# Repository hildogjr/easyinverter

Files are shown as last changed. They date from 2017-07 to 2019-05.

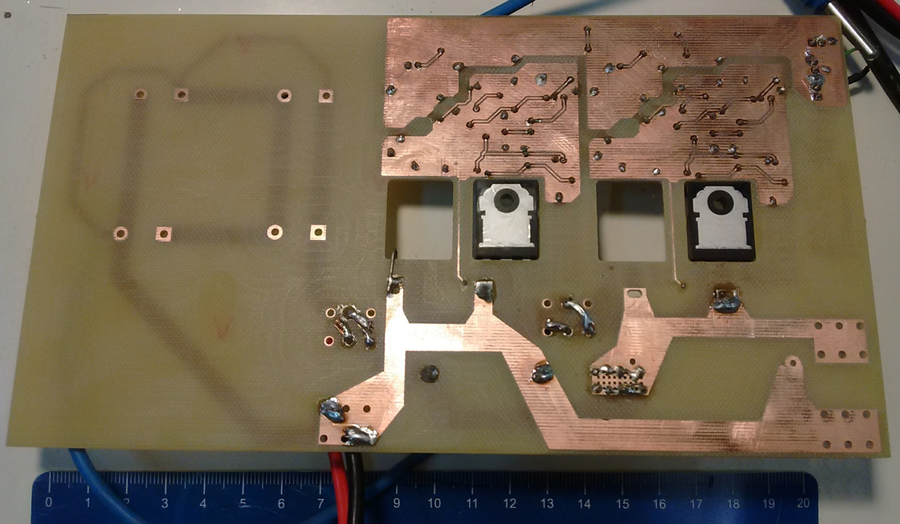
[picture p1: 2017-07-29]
prj v1/Assemblies/2017-03-13 One phase prototype [HGJr]/2017-04-28_OnePhase2(bottom).jpg

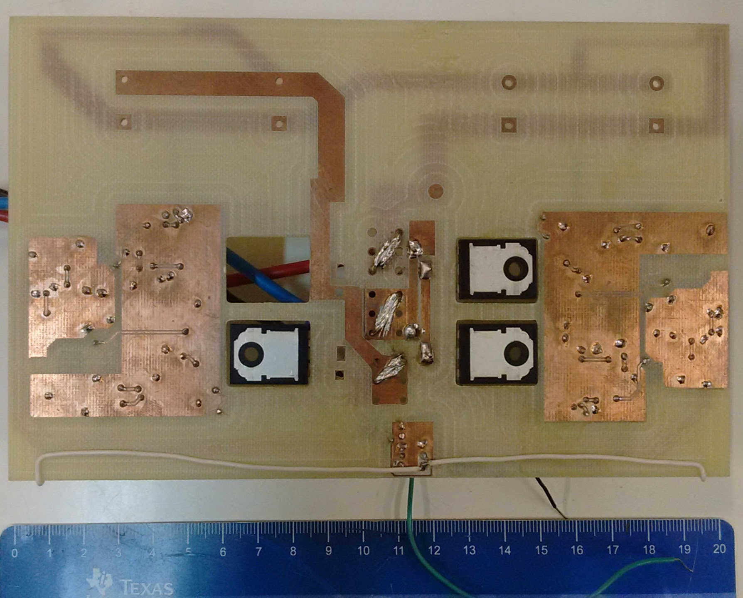
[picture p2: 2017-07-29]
prj v1/Assemblies/2017-04-03_OnePhase(bottom).jpg

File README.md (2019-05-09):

# EasyInverter
**An academic budget cost modular 4 arms inverter focused to use in researches**

Initial development by Power Conditioning Laboratory (*[Laboratório de Condicionamento da Energia Elétrica](http://www.fee.unicamp.br/dse/antenor/lcee)*), [School of Electrical and Computer Engineering](http://www.fee.unicamp.br/?language=en), at University of Campinas ([**UNICAMP Brazil**](http://www.unicamp.br/unicamp/english)).

The use of this project is free and conditioned to GNU General Propose License 3.0. The financial support was provide by São Paulo Research Foundation (FAPESP) under grants 2014/11720-7 and 2015/02325-0.

The publication of academics works contend results using this project if conditioned to a ACKNOWLEDGMENT and citation of this repository in the "acknowledgment part" of the article/paper.

You may use this text:
"The authors are grateful to the EdgeVerter's work team by the inverter project, which is available at <<https://github.com/hildogjr/EdgeVerter>>"

The GERBERs and schematic PDF are provided in the [Assemblies folder](/Assemblies).

The most recent files was designed using [Altium 18](http://www.altium.com/).

The Cost Bill of Materials can be updated by [``kicost -w -i BoM.xml -eda altium``](https://xesscorp.github.io/KiCost/), installing by ``python -m pip install kicost``.

---

## Max values (limitation) / general specifications
The specification values are not necessary concomitant.

- 10kW processing power;
- 600V of DC link;
- 50A in one phase;
- 200kHz switching frequency;
- 3.3V or 5V input logic control;
- Min dead-time & phase transistors interlock on-board;
- TWO extra relays;
- SMD topology with TO-247 transistor to easy replacement;
- Isolated power supplier to the gate driver (it not depends of PWM to works fine);
- Protection: under voltage of the isolated supplier (gate driver), over current, over voltage on the group of transistors and over temperature.

## Predicted powers proposes (look in power limitations)
1. 800V/10A -> To inverters grid connected applications, motor control;
2. 400V/30A -> To inverters grid connected applications, motor control;
3. 100V/100A -> DC/DC converters.

## Predicted uses, studies of
1. DC/DC converters, e.g., boost, buck, buck-boost, push-pull;
2. Power switching supplies, isolated topologies based on DC/DC converters;
3. Resonant converters;
4. Single-phase inverter, using the two first arms. Possibility to use the 3rd arm to synchronous connection to the grid and 4th to DC link boost/pre-load/discharge (discharge, pre-load and connection may be also performed by the two relays);
5. Three-phase inverter three wire connection. With possibility of extra arm to pre-load/discharge of the DC link, DC/DC boost or any extra application connected to the same DC link;
6. Three-phase inverter four wire connection (three-phase plus neutral);
7. Single-phase back-to-back inverter (to three-phase is necessary use two boards);
8. DOUBLE isolated single-phase inverters (independent DC links), to use as multilevel inverter applications;
9. Three-phase Vienna rectifier.

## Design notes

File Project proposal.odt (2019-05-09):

Projeto Inversor LCEE

RESUMO

Projeto do hardware de um inversor para ser utilizado em projetos de pesquisa no LCEE.

OBJETIVOS

1. O hardware deve ser robusto e projetado para evitar falhas e erros de operação, para tanto, deve utilizar proteções e indicar claramente ao usuário quando uma proteção for acionada, além de enviar sinal ao sistema de controle.
2. O hardware deve ser projetado para imunidade à interferência eletromagnética. Sendo todos os sinais de comando e retroação (proteção ativada) isolados da parte de potência.
3. O hardware deve ser flexível para atender, ao máximo possível, uma gama projetos de P&D encontrada no laboratório LCEE da Unicamp.
4. O hardware deve facilitar a obtenção de resultados experimentais, permitindo fácil acesso aos sinais internos (pontos de prova de tensão e corrente devem ser providos).

ESPECIFICAÇÕES

Tensão / Corrente

Proposta 1: 800V/10A

Proposta 2: 400V/30A

Proposta 3: 100V/100A

Frequencia de comutação:

Proposta 1: 200kHz

Outras propostas:

- Para mudança nas specs de tensão/corrente, trocar apenas transistores, resistores de gate e configurar proteção.
- Não utilizar circuto de bootstrap (possibilidade de acionar chave inferior e superior de modo independente).
- Auto-diagnóstico do estado da chave de potência.
- Tensão negativa para desligamento da chave.
- Possibilidade de utilização de transistores em SiC.
- Escalável / modular.
- Facilidade para conexão em diferentes aplicações, como inversor, inversor multinível, fonte chaveada etc.
- Proteção de mínimo dead-time.
- Modularidade na quantidade de braços.

MILESTONES/CRONOGRAMA

Reuniões de Alinhamento

Reunião 2 realizada dia 19/04/2016.

Reunião 3 realizada dia 06/05/2016.

Reunião 4 realizada dia 24/05/2016.

Distribuições de tarefas

Ficaram divididas as seguintes frentes para avançar o projeto:

1. Fonte isolada / driver => Responsável: Joel
2. Seleção do mosfet e proteção dos MOSFETs => Responsável: Lais
3. Circuitos lógicos e isolação => Responsável: Hildo
4. Montagem da placa anterior => Responsável: JP

Aplicações

Tendo em vista que a placa terá 4 braços de MOSFETs, abaixo são listadas as aplicações típica em que ela poderá ser utilizada. A placa possuirá 2 barramentos CC que poderão ser conectados de forma paralela ou independente, além de 2 saídas auxiliares a transistor para conexão de relês em 12V.

Para uso da descarga/pré-carga será necessário o uso de resistores externos e para o uso da chave rápida de conexão a rede, diodos externos.

1. Conversores CC/CC em geral. Exemplos: boost, buck, buck-boost, push-pull;
2. Fontes chaveadas, arquiteturas baseadas nos conversores CC/CC mais push-pull e full bridge;
3. Conversores resonantes;
4. Inversor monofásico (usando os braços A-B e com possibilidade de uso do braço C para conexão sincronizada a rede e braço N para descarga/pré-carga do barramento CC, essa última função também pode ser realizada pelos relês externos);
5. Inversor trifásico a 3 fios (com possibilidade de uso do 4º braço para descarga/pré-carga do barramento CC, por exemplo, no caso de acionamento de motores, descarregar o barramento no uso de frenagem eletromagnética);
6. Inversor trifásico a 4 fios;
7. Back-to-back monofásico (para trifásico usar duas placas);
8. Duplo inversor monofásico isolados entre si (para conexão série pelo lado CA e aplicações em multinível).

Escolha dos transistores

Definido encapsulamento TO-247

Modelos escolhidos:

Part# | Fabrica. | USD | Vds | Id | Qg | Tr+Tf

Escolha do gate driver

Modelo, corrente, tempos de atraso para a chave escolhida etc…

Opção inicial: MIC4420

Alternativas: MIC4421 (mais rápido), TC4420, MAX4420

Isolação do transistor / driver

Modelo de isoladores, tempos de atraso, etc:

Opção inicial: Si8422

Alternativa: FOD8012

Projeto da fonte do driver

Considerando:

N (número de chaves em paralelo) = 2

Vd (tensãod e alimentação do driver) = 12V

Qg (gate charge máximo por chave) = 234nC

Fs (frequencia máxima de comutação) = 200kHz

Por driver:

P = N * Vd * Qg * Fs = 2 * 12V * 234nC * 200kHz = 1,12W

Supondo que a proteção, isolação, driver, tenha consumo de 150mW, temos a potência por fonte de driver de 1,3W.

Projeto da fonte principal

Como ponto de partida, a potencia de cada fonte do driver de 1,3W, e supondo uma eficiência de 0.66 da fonte, no primário é cerca de 1,9W. Com 8 canais, são 15,2W. Mais os circuitos lógicos/ proteção na entrada, podemos estimar uns 3W. São então 18W, ou seja, precisamos cerca de 1,5A no 12V.

Prever mais 90 a 150mA máximo por saída de relê auxiliar, totalizando mais 300mA. Modelos interessantes: T9A series (90mA@12V) e automotivos em geral (140mA@12V).

Projeto térmico

Pesquisar dissipadores em www.tctbrasil.com.br. Definir temperatura do dissipador, ventilação etc.

Tentar casar dimensão de placa com um único dissipador.

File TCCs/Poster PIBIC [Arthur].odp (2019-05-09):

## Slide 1

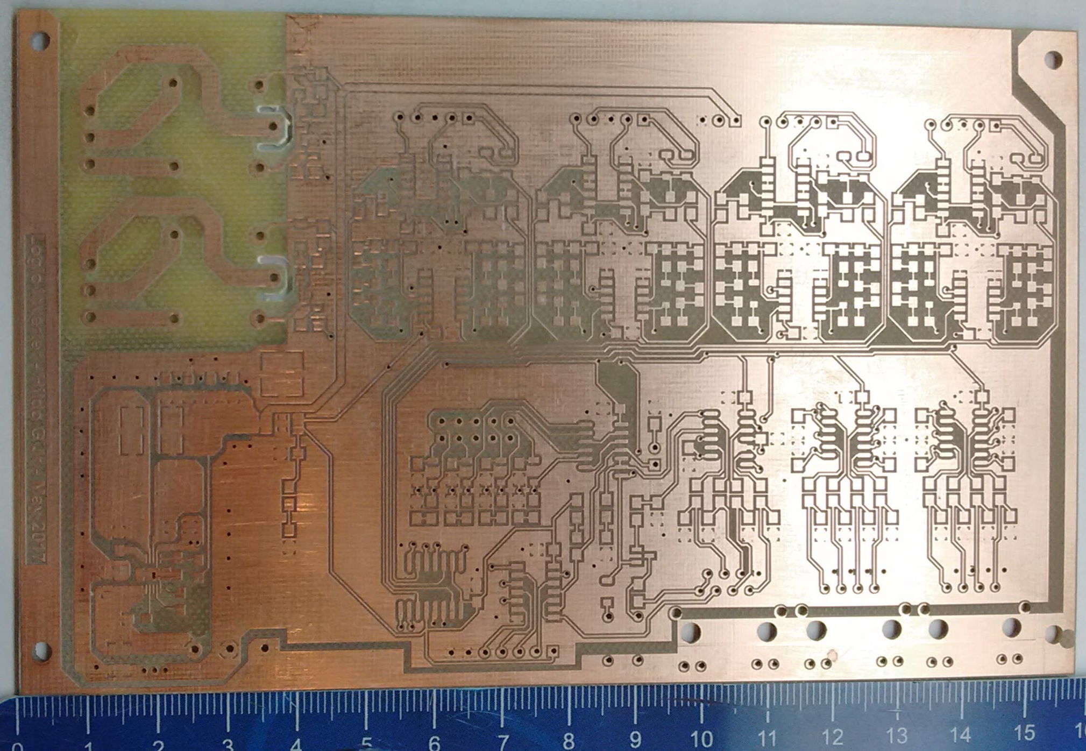
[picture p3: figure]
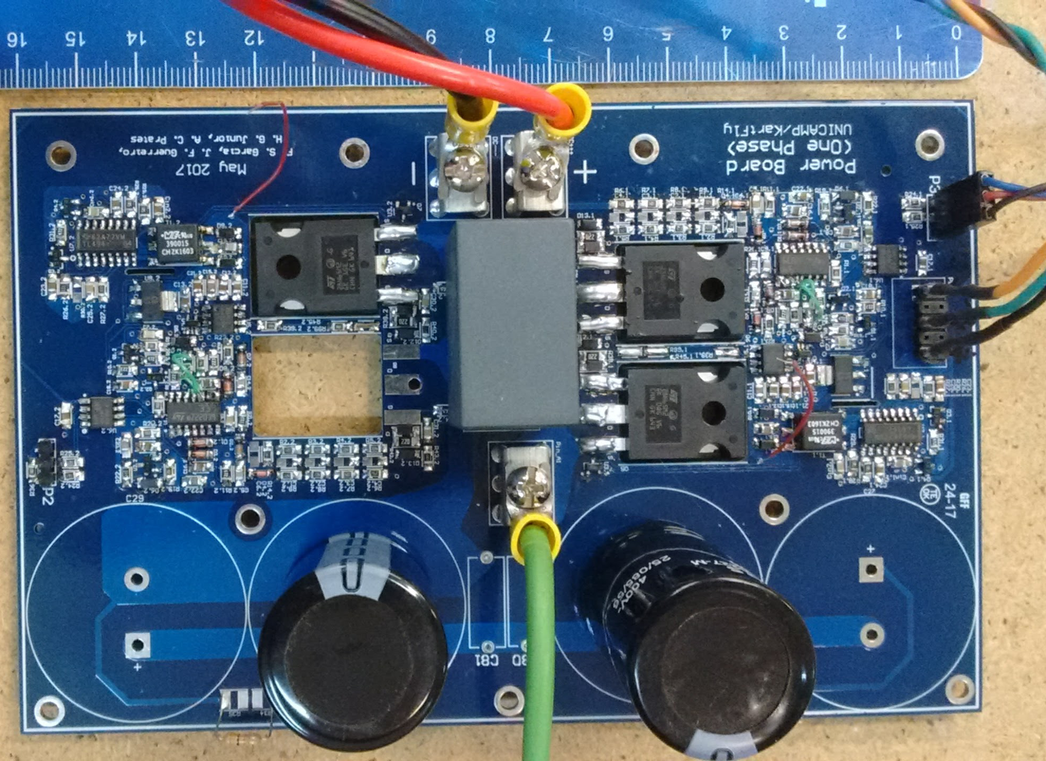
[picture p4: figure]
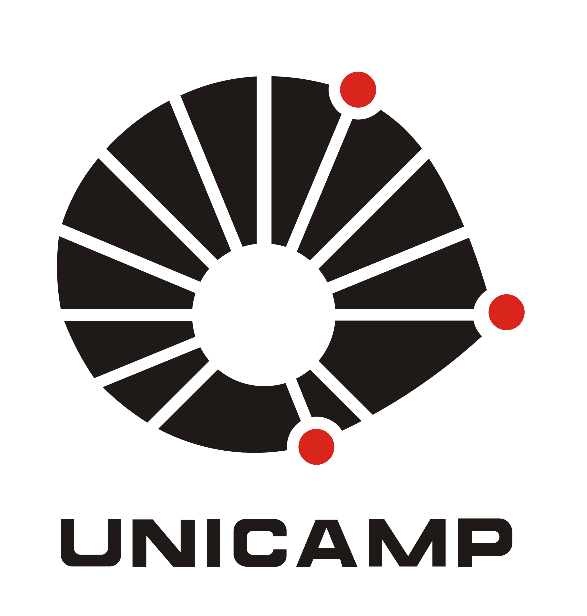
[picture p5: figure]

UNICAMP – Universidade Estadual de Campinas

FEEC – Faculdade de Engenharia Elétrica e Computação

Three-phase Inverter Development

for Distributed Generations Purpose

Arthur C. Prates, José A. Pomílio, Hildo Guillardi Jr., Joel F. Guerreiro, Fellipe S. Garcia

arthurcprates@gmail.com, antenor@fee.unicamp.br, hildogjr@dsce.fee.unicamp.br,joel.engeletrica@gmail.com,fsgarcia@gmail.com

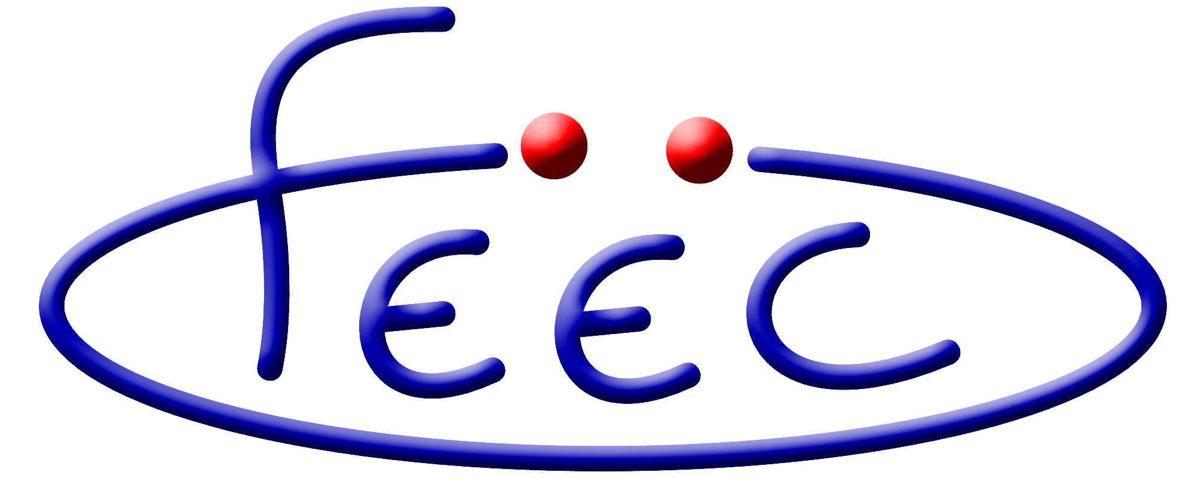
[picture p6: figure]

Key words

Power electronics, CC-CA Converter, PCB Layout, MOSFET driver

Introduction

Systems of distributed energy, based in solar panels or battery banks, need a CC-CA converter for it’s connection to the grid. The current energy regulation in Brazil aims mainly the power injection in the grid, but none is said about a better voltage profile or harmonics compensation, especially using inverters. Multi-level inverters are capable to perform these tasks due its arrangement and logic system.

As the legislation is changing is urgent the need of a open source device capable to provide the base for research in this field and prepare the new engineers.

Metodologia

The concept of the project aimed a 4 Leg inverter, capable of 800V and 200kHz switching frequency for academic researchs. The high limits are needed because of the modular concept of the whole, each module can be placed in different positions in order to achieve other topologies.

To design the concept module, the project was split in 5: Main power supply, isolated power supply, protection/gate driver and logic circuits. As a group procedure, each part was made, tested and validated separately. More informations can be get at <https://github.com/hildogjr/easyInverter> under GNU-GPL3 license.

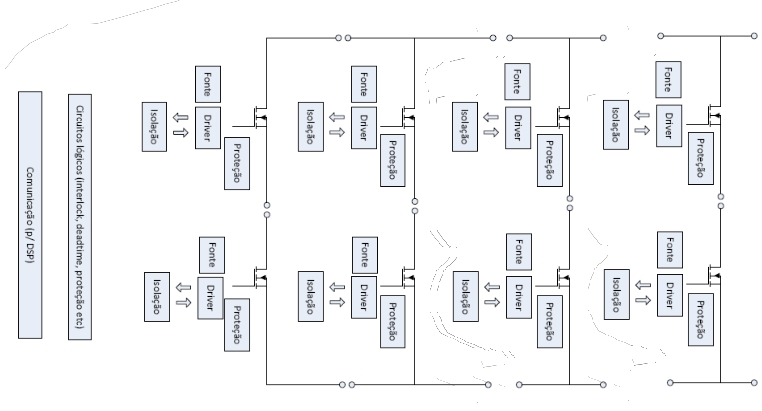
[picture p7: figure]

Figure 1. Inverter’s block diagram

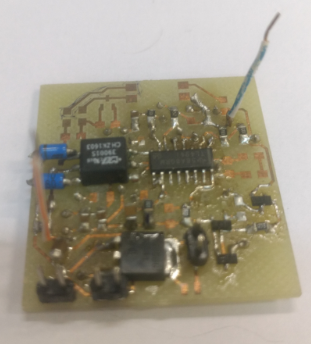
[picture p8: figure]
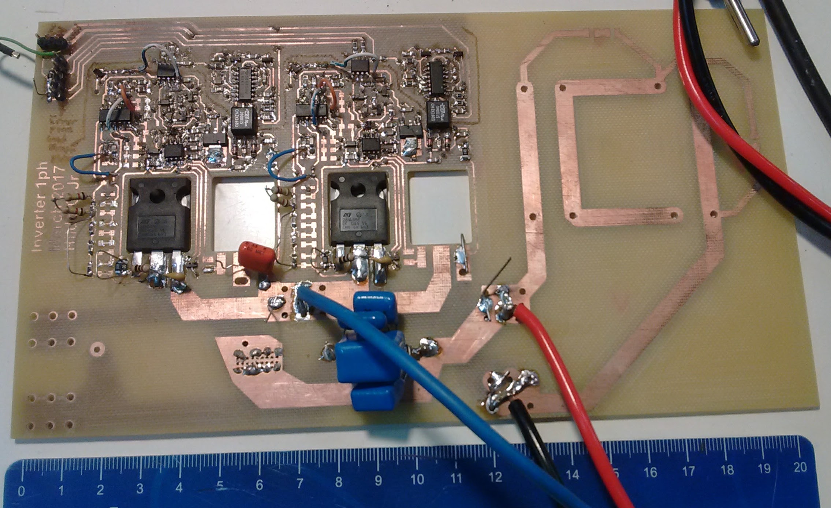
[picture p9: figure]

Figure 2. Chronology of the project

Results and Discussion

During the validation many changes and arrangements were made in order to satisfy volume, time of response and transients necessities. Also, we kept the ideia of a low cost project, designing many circuits that are found integrated in the market, but with a higher price.

The main power supply can be fed by any off the shelf notebook supplier, the protection can be adjusted acording to the choosen switching device and the driver has a snubber in order to mitigate transient ressonances.

The switching process of half bridge is shown in figure 3 by 100VDC and 78kHz. The half bridge is presented in figure 4.

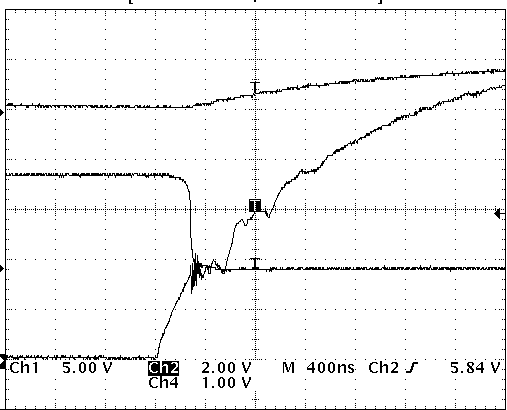
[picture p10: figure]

Figure 3. Half bridge switching at 100VDC 78kHz

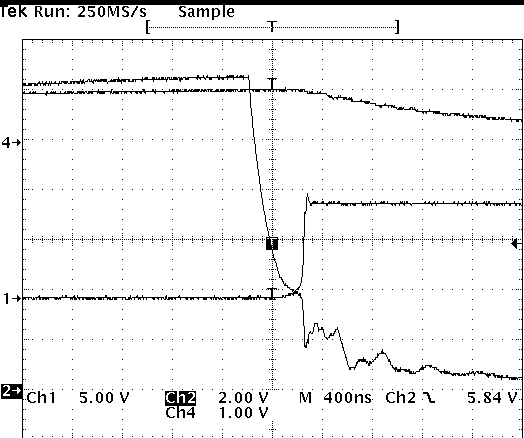
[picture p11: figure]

Figure 4. Complete half bridge module

Conclusion

The project presented itself as a challenge in many parts. Some effort still need to be done towards the ease of the noise presented in the switching phase in higher frequencies in order to allow the focus on the fine tuning of the protection and further built of the whole system.

We believe that soon we will have a functioning Inverter ready to be used and understand that some barriers take a longer time to be pushed in a state of the art project.

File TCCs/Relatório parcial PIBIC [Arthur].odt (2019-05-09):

Desenvolvimento de Inversor Trifásico para Aplicações em Sistemas de Geração Distribuída

1. Resumo das atividades

O projeto de iniciação científica proposto tem como o objetivo o desenvolvimento de um inversor de frequência open source para uso didático nos laboratórios da Faculdade de Engenharia Elétrica e Computação. É visado um projeto capaz de admitir diferentes tipos de topologias de montagem, diferentes tipos de dispositivos (Mosfets, IGBTs) e diferentes lógicas de funcionamento, sem perda de didática e compreensão dos layouts implementados.

Para tal tarefa, foi montado um Grupo de Trabalho composto por 4 pessoas com diferentes backgrounds, além da supervisão do Prof. Dr. José Antenor Pomílio. Entre as tarefas que tenho desempenhado estão: Layout de protótipos com o software Altium, testes de desempenho e preparo do memorial descritivo do projeto.

Em um primeiro momento foi definido que o esquema de funcionamento do inversor seria como representado na Figura 1, tendo um lógica central, sistema de intertravamento, fonte principal, gate drivers, com suas respectivas fontes isoladas, além dos MOSFETs em si.

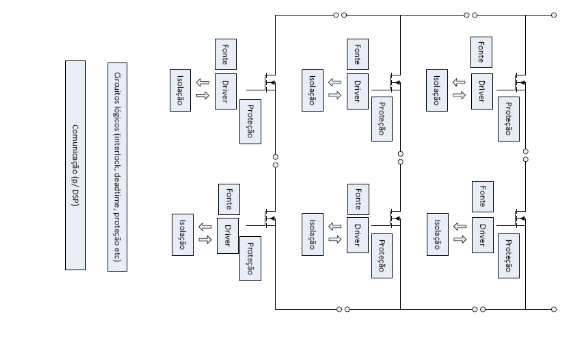
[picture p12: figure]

Figura 1. Proposta inicial do funcionamento do circuito

O desenvolvimento do projeto segue um modelo modular de desenvolvimento e teste, de forma que cada bloco representado na figura 1 teve seu layout a parte do todo, possibilitando o desenvolvimento de protótipos e seus testes específicos, buscando assim a redução do acúmulo de erros do projeto final mais complexo.

Como modelo inicial, tinhamos o seguinte cronograma, seguindo a tabela 1:

1. Estudo do circuito e das características dos componentes

2. Pesquisa bibliográfica sobre aspectos de “layout” em circuitos eletrônicos de potência

3. Desenvolvimento de simulações e “layout” do circuito

4. Estudos térmicos

5. Montagem do protótipo

6. Testes funcionais

7. Relatório

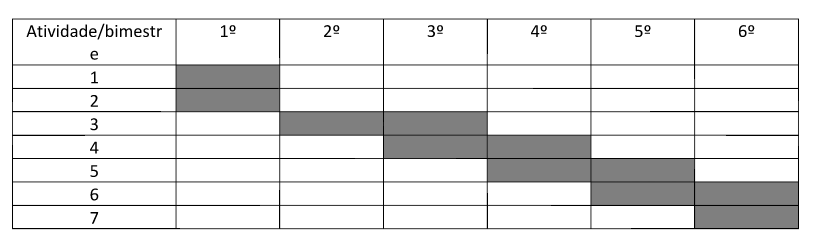
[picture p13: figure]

Tabela 1 . Representação das etapas do cronograma

As etapas 1, 2 estão completas, a etapa 3 foi reduzida para apenas “layout do circuito”, uma vez que as simulações não foram necessárias, sendo substituídas pela etapa 5 - montagem de protótipo - e pela etapa 6 - testes funcionais.

A etapa 4 foi analisada quanto a escolha do posicionamento do dissipador de calor e a orientação dos mosfets no layout em relação a ele.

As tarefas até o momento podem ser descritas como apresentadas na tabela 2.

Tarefa | Estado atual
Estudo do circuito e das características dos componentes | Concluído
Pesquisa bibliográfica sobre aspectos de “layout” em circuitos eletrônicos de potência | Concluído
Design e layout do circuito | Concluído parcialmente
Estudos térmicos | Concluído
Montagem do protótipo | Concluído parcialmente
Testes funcionais | Concluído parcialmente

Tabela 2. Representação do estado atual das tarefas

2.Desenvolvimento do conjunto

Os layouts de circuito apresentados são SMD a fim de proporcionar uma melhor dissipação de calor, uma vez que o dissipador será preso à parte inferior da placa final e componentes do tipo Through-hole seriam um empecilho para o paralelismo das superfícies. Uma análise mais detalhadas das etapas descritas acima segue.

2.1 Boas práticas de layout

Para o início das atividades de diagramação e layout de circuitos eletrônicos foi desenvolvido um pequeno manual de boas práticas de layout. Os pontos abordados são a necessidade da existência de um plano de terra, a separação entre circuitos analógicos e digitais, a existência de trilhas que possam se tornar antenas ou pontos de alta impedância. Mais detalhes constam no documento Check list :Boas práticas de Design.

2.2 Design, layout do circuito, protótipos e testes

2.2.1 Buck

Desenvolvimento de um circuito regulador de tensão com entrada variável de 14 a 36V e saída de 12V a fim de alimentar todo o circuito. Dimensionado para 24W e corrente de 2A de saída .

O desenvolvimento do projeto se iniciou pelo dimensionamento da alimentação principal. Um circuito Buck, com entrada variável e saída fixa de 12V. Essa tensão de saída foi posteriormente redefinida para 10 V, por motivos que serão apresentados abaixo.

2.2.2 Fonte Isolada

O desenvolvimento da fonte isolada levou certo tempo, por envolver decisões definitivas de conceito de funcionamento do todo. Partindo do ponto que ela teria potência de 1W. entrada de 12V e output de 12V e 5V isolados fizemos o primeiro diagrama, contendo circuitos limitadores de corrente e de controle de tensão a fim de estabilizar a saída, no caso de variações bruscas da corrente de saída.

Ao desenvolver o primeiro layout e testar o protótipo, foi notado a não necessidade dos circuitos limitadores de corrente e controle de tensão para as aplicações que a fonte isolada seria usada. Assim conseguimos passar do layout da figura 2 para o layout da figura 3.

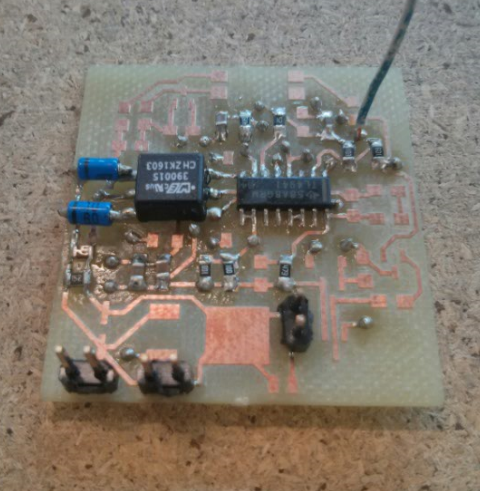
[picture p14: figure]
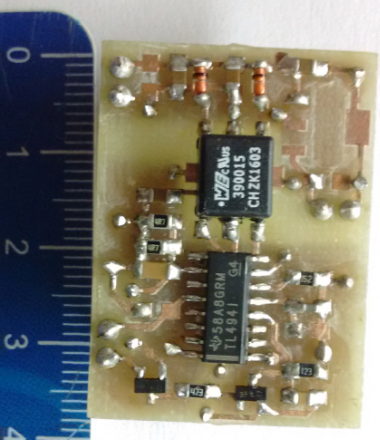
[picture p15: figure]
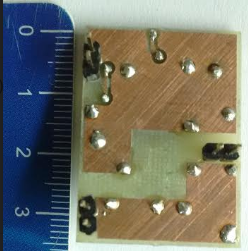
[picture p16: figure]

Figura 2. Primeiro protótipo da fonte isolada, com proteções contra surto de corrente e variação de tensão | Figura 3. Versão final da fonte isolada, com planos de terra bem definidos e separados

Questionamentos sobre posição de entrada e saída fizeram toda a diferença na definição do último design. Outros layouts foram sugeridos entre o primeiro e o final, contudo o posicionamento da estrada - lado esquerdo inferior figura 3 e posicionamento da saída - lado direito superior figura 3- se mostraram os mais interessantes, por possibilitar uma boa separação dos planos de terra, aumentando a confiança na isolação dos dois circuitos, além de colocar o transformador como a única conexão entre circuito isolado e não isolado.

Uma mudança crucial para a manutenção das dimensões do circuito relativamente pequena foi a mudança da alimentação da fonte e do transformador smd de 1:1 para 1:1.2.

Transformadores tem uma característica construtiva analisada como dV/dt. O circuito da fonte isolada tem o TL494 como CI principal que faz o controle de PWM do circuito, chaveando a tensão de entrada em pulsos de onda quadrada que seguem para o transformador e depois são ratificados pelos diodos de saída. A transição entre nível baixo da onda quadrada para o nível alto ocorre num espaço pequeno de tempo, que resulta na necessidade de dimensionar o dV/dt. Para valores de variação de tensão no tempo maiores que a nominal do transformador existe a possibilidade que ele sature e acabe drenando mais corrente que a fonte suporta, queimando o circuito.

Reduzindo a tensão de alimentação de 12V para 10V garantimos que o valor dV/dt fique abaixo do nominal,evitando a saturação do transformador, sendo necessário apenas a troca do transformador para um de relação de espiras 1:1.2.

Quando submetido a testes, observamos um comportamento atípico da fonte isolada em circuito a vazio. O oscilador do CI apresentava gitter como mostrado na figura 4 e a saída do transformador não apresentava um sinal de PWM como mostrado na figura 5.

Seguindo a análise, percebemos que isso só ocorria para situações a vazio pelo CI entrar em modo stand-by. Para cargas pequenas (maiores que 1k) o circuito se comporta de forma estável.

Outro ponto observado foi que a potência de 1W é a máxima possível. Para valores maiores, a tensão de saída cai para 2V.

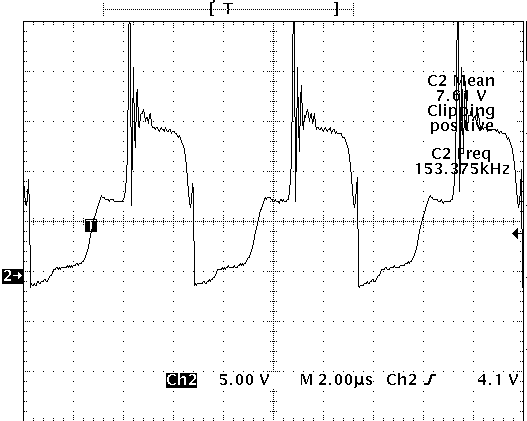
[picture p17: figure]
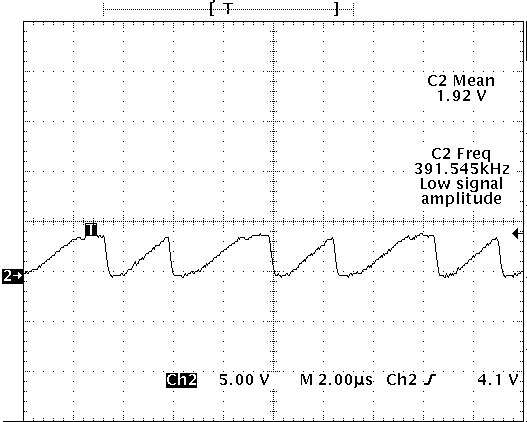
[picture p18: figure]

Figura 4. Representação da saída do oscilador com fonte a vazio. | Figura 5. Representação da saída do transformador com fonte a vazio.

2.2.3 Gate Driver e Proteções

O circuito de acionamento de mosfets representado na figura 6 foi feito de forma modular e conta com 3 tipos de proteção - tensão de desligamento, corrente e temperatura - sendo que muitas delas dependem de um ajuste fino dos resistores para um funcionamento ideal. Para tanto, foi desenvolvido uma planilha no excel que calcula a proteção obtida a partir dos valores de capacitores e resistores utilizados. De modo empírico é possível chegar aos valores de proteção desejados a partir da tabela.

O layout foi desenvolvido primeiramente separado da fonte isolada e posteriormente um braço do inversor foi roteado. No momento, estamos desenvolvendo testes para o protótipo de um braço.

Como é possível ver na figura 6, o esquema possui um optoacoplador de alta velocidade, responsável por mandar e receber os sinais da/para lógica central. A placa com uma fase está na figura 7.

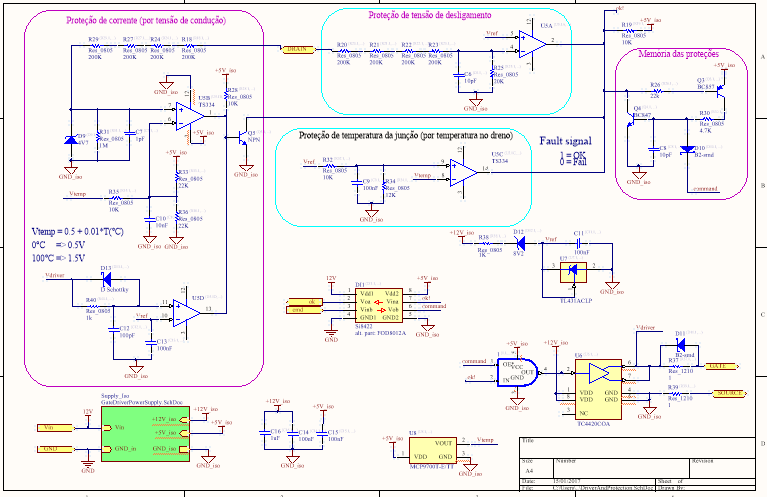
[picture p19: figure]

Figura 6. Representação do circuito Gate driver e proteções

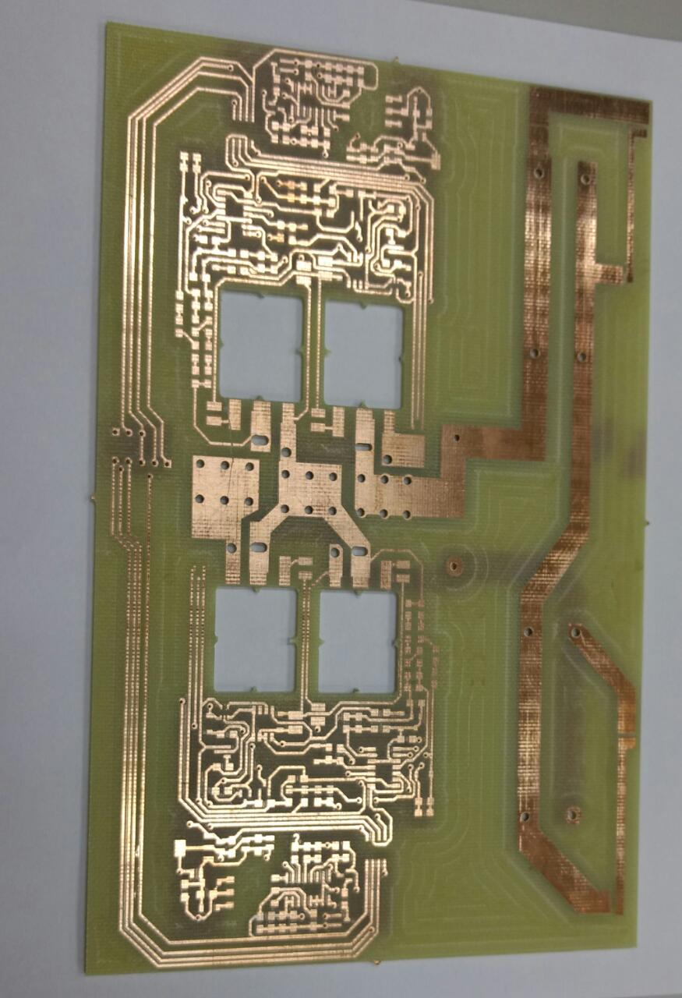
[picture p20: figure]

Figura 7. Protótipo de uma fase do inversor.

2.2.4 Lógica Central e Dead Time

A lógica central, figura 7, é responsável por gerenciar os possíveis erros que possam causar o mau funcionamento do inversor. O circuito de proteção atua na detecção de erros, os enviando para o circuito de lógica a fim da proteção atuar. Toda a lógica prevista é analógica, com portas lógicas e buffers. Para uma atuação mais ágil sem que o sinal de erro precise percorrer todo o caminho até a lógica central, existe um circuito de permissão junto ao gate driver que permite ou não seu acionamento, a partir dos sinais das proteções (sinal de ok! Na porta And, figura 6).

O circuito de Dead Time existe para que os mosfets do mesmo ramo não sejam ligados simultaneamente, curto-circuitando o barramento.

3. Próximos passos

Para o encerramento do projeto é necessário a finalização do roteamento do circuito de lógica e dead time e a execução do conjunto completo, para a validação do inversor como um dispositivo operante.

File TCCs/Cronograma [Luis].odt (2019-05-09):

Ok | Data | Etapa
X | 01 – 10 Fev | Revisão do Projeto
X | 10 Fev – 12 Mar | Montagem e ensaios na placa antiga
| 12 Mar – 22 Mar | Revisão bibliográfica de Mosfets e Driver - Efeitos adversos, ringing e recuperação reversa
| 22 Mar – 10 Abril | Correções do esquemático / Bibliotecas
| 10 Abril – 17 Abril | Layout 1 Driver
| 17 Abril – 24 Abril | Etapa de conferência de erros (Joel e Hildo)
| 24 Abril – 30 Abril | Layout de um braço (ponte H na nova definição)
| 30 Abril – 07 Maio | Etapa de conferência de erros
| 07 Maio – 17 Maio | Layout 4 braços
| 17 Maio – 24 Maio | Etapa de conferência
| 24 Maio – 07 Junho | Confecção e montagem / Inicio de redação TCC
| 07 Junho – 30 Junho | Testes e validação
| …. | Redação do TCC
| | Finalização do Inversor de 4 braços . SIC etc
| | Documentação (datasheet)

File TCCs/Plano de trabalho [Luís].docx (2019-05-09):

UNIVERSIDADE ESTADUAL DE CAMPINAS

FACULDADE DE ENGENHARIA ELÉTRICA E DE COMPUTAÇÃO

LABORATÓRIO DE CONDICIONAMENTO DE ENERGIA ELÉTRICA - LCEE

EA006 – TRABALHO DE FIM DE CURSO

JULHO 2018

ESTUDO SOBRE PROBLEMAS DE COMPATIBILIDADE ELETROMAGNÉTICA EM UM INVERSOR DE ALTA FREQUÊNCIA

Aluno:

Luís Henrique D’Ávila Possatti

RA: 147098

e-mail: luis.possatti@gmail.com

Orientador:

Prof. Dr. José Antenor Pomilio

Tel. : (19) 3521.3708

e-mail: antenor@fee.unicamp.br

Coorientadores:

Hildo Guillardi Júnior

hildogjr@dsce.fee.unicamp.br

Joel Filipe Guerreiro

joel.engeletrica@gmail.com

(19) 3521-0245

# Introdução

A geração de energia elétrica através de fontes renováveis e de forma distribuída, como solar e eólica, vem ganhando crescente atenção da comunidade acadêmica e da sociedade no geral. Uma das tecnologias chave para que esse tipo de aplicação seja possível é o inversor de frequência, que permite a conversão de energia elétrica disponibilizada na forma de tensão contínua para a forma de tensão alternada senoidal. O esquemático básico desse tipo de circuito é mostrado na Figura 1.

Com esse tipo de circuito, é possível conectar uma string de painéis solares e utilizá-la como fonte, fazendo o papel de Vd no esquemático abaixo, e fazer com que sua energia seja injetada na rede elétrica que é conectada nas saídas fase A, fase B e fase C. Se a fonte de energia fosse um gerador eólico, a energia por ele produzida é entregue na forma alternada e tipicamente possuí frequência que varia com a velocidade do vento. Nesse caso, a tensão é retificada e então conectada na entrada do inversor, cuja saída é conectada na rede da mesma forma que no caso da energia solar.

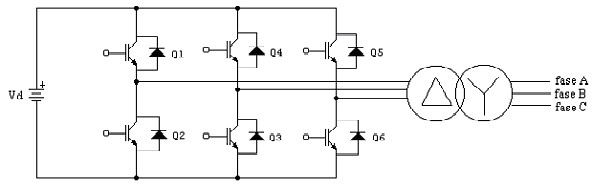
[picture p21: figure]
Image result for inversor de frequencia esquematico

Figura 1: Esquemático de um circuito inversor utilizando IGBTs.

Outra aplicação típica é utilização de um inversor de frequência no controle de motores de indução. Além disso, pode utilizar apenas um ou dois braços desse circuito para outras aplicações, como um conversor CC-CC abaixador de tensão (Figura 2) ou controle de motores CC (Figura 3).

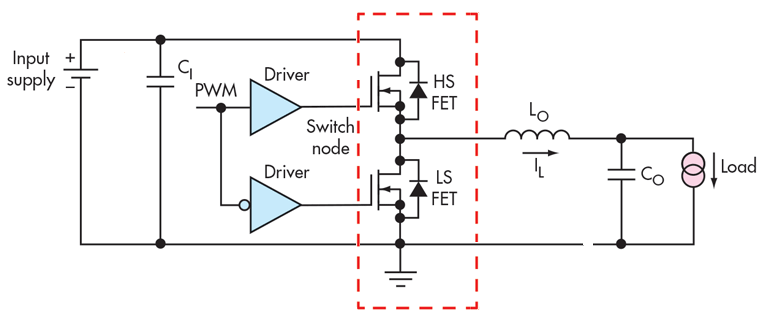
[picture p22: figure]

Figura 2: Circuito do conversor CC-CC com destaque para a utilização de um dos braços do inversor.

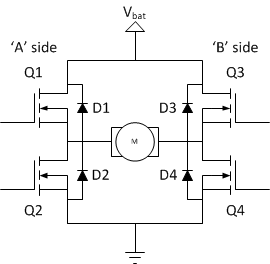
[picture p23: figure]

Figura 3: Circuito de um controlador de motor CC utilizando dois braços de um inversor.

Como se pode perceber, o circuito de um inversor possui diversas aplicações. Por isso, o Laboratório de Condicionamento de Energia Elétrica (LCEE) possui uma plataforma desse tipo, muito robusta, construída faz alguns anos. Entretanto, devido às limitações tecnológicas da época em que foi concebido, não é capaz de atender a aplicações de tensão e frequência de comutação mais elevadas. Dessa forma, é de interesse do LCEE o desenvolvimento de uma nova versão de inversor, que tenha a capacidade de ser alimentado com tensão de até 800 V, frequência de chaveamento de até 200 kHz e que consiga fornecer até 10A.

Com esse novo projeto, será possível explorar projetos de pesquisa que trabalhem com tensões mais elevadas e a alta frequência de chaveamento permitirá que sejam utilizados menores indutores e capacitores nas aplicações que fizerem uso do sistema. Além disso, percebeu-se que é relativamente difícil encontrar inversores com essas especificações no mercado e, quando encontrado, o mesmo apresenta um custo muito elevado. Sendo assim, há um objetivo de desenvolver um projeto open-hardware de custo baixo que, após a conclusão e validação, seja disponibilizado para a comunidade acadêmica.

# Resultados preliminares

Encontra-se em desenvolvimento um projeto de validação que compreende apenas um braço do inversor. A Figura 4 representa o diagrama de blocos do circuito construído. A validação desse projeto revelou alguns problemas de funcionamento, os quais serão expostos a seguir. O objetivo deste trabalho de conclusão de curso é propor modificações no projeto atual para solucionar tais problemas.

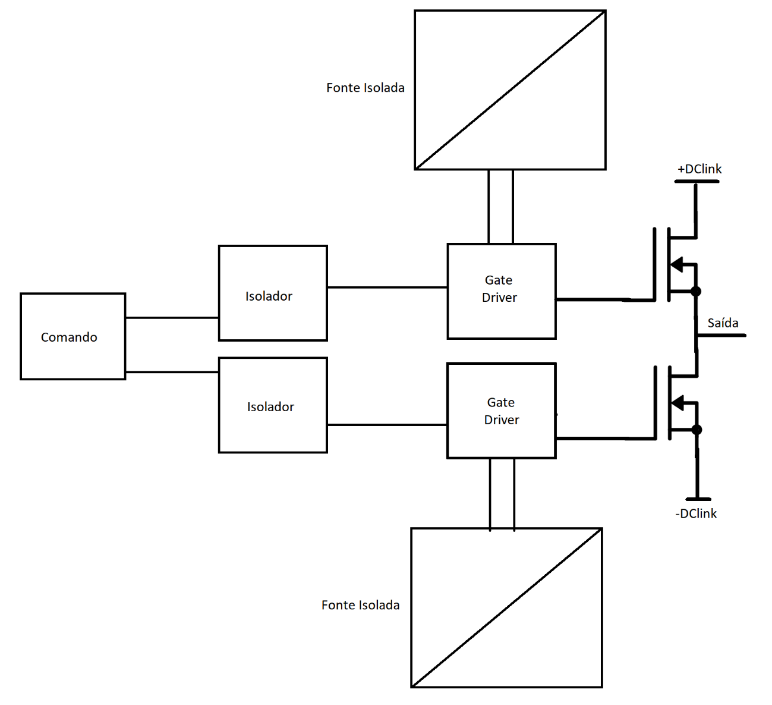
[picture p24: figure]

Figura 4: Diagrama de blocos do projeto de validação.

Os testes mostrados a seguir foram realizados colocando uma carga RL e acionando os MOSFETs com sinais PWM complementares. Observou-se que quando a corrente era comutada de um transistor para o outro, apareciam oscilações de tensão de amplitude relativamente altas em diversas partes do circuito. As imagens a seguir reproduzem alguns dos resultados.

A Figura 5 mostra que a tensão gate-source do MOSFET oscila com uma frequência elevada (aproximadamente 100 MHz) quando a mesma ultrapassa o limiar de 4V que representa o início da sua condução.

A Figura 6 apresenta o comportamento da tensão de alimentação do driver do MOSFET no mesmo momento que foi analisado na Figura 5. Quando o transistor é comutado, essa tensão oscila em torno do seu valor de regime permanente, 15 V, atingindo um vale próximo a 0 V.

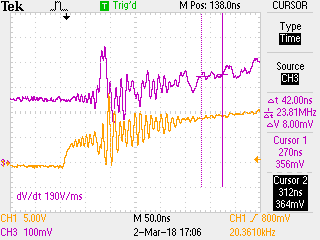
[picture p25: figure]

Figura 5: Tensão Vgs (amarelo) e corrente da carga (rosa).

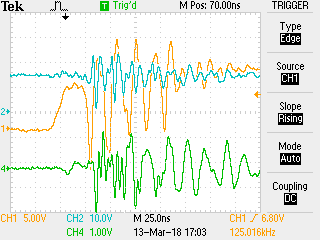
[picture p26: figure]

Figura 6: Tensão Vgs (amarelo) no MOSFET 1, tensão de alimentação do driver (azul) e Vds do MOSFET 2(verde).

A Figura 7 mostra a oscilação presente na tensão CC e na corrente da carga quando ocorre a comutação dos MOSFETs.


Figura 7: Tensão do barramento CC (amarelo) e corrente da carga (rosa).

Os resultados reproduzidos acima foram obtidos com uma tensão CC próxima de 80 V. Observou-se que amplitude das oscilações tem forte dependência da tensão comutada pois, ao elevá-la além de certo nível, aproximadamente 60 V, as oscilações intensificavam-se. Abaixo desse nível, eram praticamente inexistentes.

Quando essas oscilações se tornavam grande o suficiente, os circuitos de proteção contra sobrecorrente e sobretensão, implementados de forma analógica, disparavam sinais de erros do tipo falso-positivo, desabilitando o inversor. Isso se deve ao fato de que a tensão de alimentação desses circuitos analógicos também se desestabiliza, induzindo-os assim a comportamentos não esperados.

Além disso, observou-se que quando se eleva e a tensão e a corrente a valores um pouco maiores do que os mostrados na Figura 7, o sistema é levado a falhas catastróficas, com a destruição dos transistores. Nos ensaios realizados, o limite máximo de potência processada pelo inversor foi na condição de operação com 200 V de alimentação e corrente de carga de 1 A.

# Objetivo

Como é possível observar pelo que foi apresentado na seção anterior, o projeto atual não atinge a performance que foi proposta em sua concepção. Portanto, é necessário fazer estudos e modificações no mesmo, o qual serão os objetivos do Trabalho de Fim de Curso aqui apresentado.

Nesse trabalho, o aluno buscará estudar hipóteses para explicar as causas dos problemas apresentados e propor modificações na busca de melhores resultados. O enfoque principal será na resolução do problema das oscilações que ocorrem durante o chaveamento dos MOSFETs, especialmente na alimentação do gate driver e na tensão gate-source.

Serão analisadas as seguintes questões:

- Compatibilidade eletromagnética:
  - Topologias de filtragem,
  - Otimização de layout da Placa de Circuito Impresso[1],
  - Possíveis interferências causadas pelo dissipador de calor[2],
- Adição de ferrite para supressão de oscilações de alta frequência[3];

# Referências

1. Armstrong, K. (21 de Maio de 2009). EMC techniques in electronic design Part 5 - Printed Circuit Board (PCB) Design and Layout. Acesso em 11 de Julho de 2018, disponível em https://www.emcstandards.co.uk: https://www.emcstandards.co.uk/files/part_5_text_and_graphics_21_may_09.pdf
2. Armstrong, K. (Julho de 2010). EMC Techniques for Heatsinks. (EMC Standards) Acesso em 11 de Julho de 2018, disponível em https://www.emcstandards.co.uk: https://www.emcstandards.co.uk/files/emc_techniques_for_heatsinks_july_2010.pdf
3. Jonathan Dodge, P. (25 de Março de 2004). Eliminating Parasitic Oscillation between Parallel MOSFETs. Application Note APT-0402, pp. 1-6.
4. Klein, J. (25 de Abril de 2003). AN-6003 - “Shoot-through” in Synchronous Buck Converters. Acesso em 11 de Julho de 2018, disponível em https://www.fairchildsemi.com/application-notes/AN/AN-6003.pdf

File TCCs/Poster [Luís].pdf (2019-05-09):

### RESULTADOS X DISCUSSÃO

### METODOLOGIA

### CONCLUSÃO

### RESULTADOS PRELIMINARES

### INTRODUÇÃO

### REFERÊNCIAS

## APERFEIÇOAMENTO DO PROJETO DE UM INVERSOR DE FREQUÊNCIA

TRABALHO DE CONCLUSÃO DE CURSO – ENGENHARIA ELÉTRICA

Luís Henrique D’Avila Possatti, Hildo Guillardi Júnior (co⁻orientador), Joel Filipe Guerreiro (co⁻orientador) e José Antenor Pomilio (orientador)


Nos testes realizados na primeira versão do projeto, apresentaram-se problemas relacionados a oscilações de alta frequência, geradas durante o processo de chaveamento dos transistores, as quais se espalhavam por diversos pontos da placa, inclusive para a alimentação do circuito de disparo de gate e da eletrônica de proteção, conforme se verifica na Figura 3, Figura 4 e Figura 5.
Ao atingirem-se tensões de operação ligeiramente superiores a 100V, ocorria a destruição dos transistores através do rompimento de seus encapsulamentos.

Criaram-se hipóteses para se explicarem os problemas apresentados nos testes iniciais e, através delas, desenvolveram-se propostas de melhorias para a segunda versão do projeto. Sustentou-se a ideia de que as intensas variações de tensão no source do MOSFET M2 geravam correntes de modo comum que circulavam para o terra de alimentação da placa de gatedriver através dos acoplamentos capacitivos do transformador da fonte isolada. Essas correntes produziam oscilações ao percorrer as trilhas e planos de alimentação desses circuitos.

A geração de energia elétrica através de fontes renováveis e de forma distribuída, como solar e eólica, vem ganhando crescente atenção da comunidade acadêmica e da sociedade no geral. Uma das tecnologias chave para que esse tipo de aplicação seja possível é o inversor de frequência, que permite a conversão de energia elétrica disponibilizada na forma de tensão contínua para a forma de tensão alternada senoidal.
Há alguns anos, desenvolveu-se um inversor no Laboratório de Condicionamento de Energia Elétrica (LCEE). Embora o projeto seja robusto, sua atualização é necessária pela crescente demanda por maiores especificações de tensão, corrente e frequência de chaveamento, devido às pesquisas realizadas atualmente no laboratório.

A partir dos resultados obtidos, concluiu-se que um dos grandes problemas da primeira versão fora eliminado, tornando-se, agora, a tensão, dos circuitos de disparo de gate e de proteção, estável. Embora outros principais problemas ainda não tenham sido totalmente resolvidos, o presente estudo é uma contribuição importante no entendimento dos processos de falha de um inversor e possibilitou a compreensão de que a indutância parasita nas trilhas que ligam a placa de gatedriver ao pino dos MOSFETs contribui para a instabilidade da tensão VGS,
tanto para o transistor sobre processo de disparo quanto para o seu complementar, como se mostra na Figura 19 e Figura 20.

Figura 1: Diagrama de blocos do inversor.

Figura 2: Esquemático do teste realizado em laboratório. | Figura 3: Tensão VGS de M2 (amarelo) e corrente da carga (rosa). | Figura 4: Tensão VDS de M2 (amarelo) e corrente da carga (rosa).

Figura 5: Tensão VGS de M2 (amarelo) e tensão de alimentação do driver (azul).

Figura 6: Tensão VGS de M1 (amarelo) e corrente da carga (rosa). | Figura 7: Fotografia da placa após teste que levou ao rompimento do encapsulamento dos transistores.

Figura 8: Modelo do circuito da fonte isolada, incluindo capacitâncias parasitas de seu transformador, alimentando gatedriver do MOSFET highside.

Figura 9: Modelo do novo circuito de fonte isolado proposto, utilizando common mode choke para bloquear correntes de modo comum.

Figura 10: Ilustração do princípio de funcionamento de um common mode choke.

Figura 11: Modelo do circuito de gatedriver incluindo capacitâncias CGS e CGD do MOSFET e indutância parasita das trilhas da placa.


Figura 12: Resultado da simulação SPICE para tensão VGS de M1 durante chaveamento de M2, desconsiderando indutância parasita no circuito de disparo.


Figura 13: Resultado da simulação SPICE para tensão VGS de M1 durante chaveamento de M2, considerando indutância parasita no circuito de disparo.

Figura 14: Modelo 3D da montagem do inversor, explicitando a divisão entre placa base com transistores de potência e placas de gatedriver, montadas na vertical.

Figura 15: Modelo 3D da montagem do inversor, explicitando distância entre conexões da placa de gatedriver e pinos dos MOSFETs.

Figura 19: Tensão VDS (amarelo) e VGS (verde) do MOSFET highside e forma de onda da corrente de gate (vermelha) obtida através da medição da tensão sobre resistor de gate. Tensão do link CC de 35 V.

Figura 20: Tensão VDS (amarelo) e VGS (verde) do MOSFET. Tensão do link CC de 35 V.

Figura 21: Corrente de gate e diferença entre a tensão VGS medida na saída da placa de gatedriver e nos pinos do MOSFET.

Figura 19: Tensão de alimentação da placa de gatedriver soldada sem common mode chokes e capacitor C5 da Figura 9.

Figura 17: Tensão de alimentação da placa de gatedriver soldada com common mode chokes e capacitor C5 da Figura 9.

Figura 18: Tensão de alimentação do driver durante utilização do inversor com tensão de link CC de 35V.

Além disso, conjecturou-se que a destruição dos MOSFETs, quando o inversor é alimentado por altas tensões, está relacionada com a ocorrência de curtos de braço durante a comutação de um dos transistores.
Realizaram-se simulações em SPICE mostrando que pulsos de tensão são gerados na junção gatesource de M1 durante o disparo de M2, devido à variação de sua tensão VDS e à presença das capacitâncias CGD e CGS, conforme mostrado na Figura 11.
Na Figura 12, mostra-se o resultado para a simulação quando
se despreza a indutância Lstray, que representa uma indutância
parasita no circuito de disparo de gate. Já na Figura 13, mostra-se o resultado da simulação considerando-a no circuito.

Soldaram-se duas placas gatedriver. Uma, com o circuito proposto da Figura 9 e outra, sem os common mode chokes e o capacitor C5. Alimentou-se a placa com uma fonte de bancada e mediu-se a tensão de entrada. Os resultados são mostrados na Figura 16 e Figura 17. Observam-se intensos picos de tensão na versão na qual os componentes não foram soldados, indicando-se que o chaveamento da próprio transistor do conversor já é capaz de criar correntes de modo comum através de seu transformador. Na Figura 18, mostra-se que a interferência na tensão de alimentação do driver foi resolvido na segunda versão do projeto. Essa imagem foi obtida com o inversor chaveando a uma frequência de 20kHz e com uma tensão de alimentação do link CC de 35V, utilizando-se a placa gatedriver com filtros de modo comum.
Na Figura 19, mostra-se que, embora as oscilações estejam menos intensas, ainda ocorrem perturbações na tensão VGS quando há ringing na tensão de saída. Esse fenômeno pode ser explicado pela indutância parasita representada na Figura 11, cuja presença é evidenciada na Figura 21, que mostra corrente de gate e a diferença entre a tensão VGS medida na saída da placa de gatedriver e diretamente nos pinos do MOSFET.
[1] ST Microelectronics, “STW28N65M2 datasheet,” Dezembro 2014. [Online]. Available: https://www.st.com/resource/en/datasheet/stw28n65m2.pdf. [Acesso em 01 Novembro 2018].
[2] VISHAY SILICONIX, “Power MOSFET Basics: Understanding the Turn-On Process - Application Note AN850,” 2015. [Online]. Available: https://www.vishay.com/docs/68214/turnonprocess.pdf. [Acesso em 31 Outubro 2018].
[3] Toshiba Electronic Devices & Storage Corporation, “Parasitic Oscillation and Ringing of Power MOSFETs,” 2018. [Online]. Available: https://toshiba.semiconstorage.com/info/docget.jsp?did=59456. [Acesso em 31 Outubro 2018].
[4] R. Brewer, “What is Differential and Common Mode Current?,” 2 Agosto 2012. [Online]. Available: https://interferencetechnology.com/what-is-differential-and-common-mode-current/. [Acesso em 1 Novembro 2018].
[5] ON Semiconductor, “Methods to Identify Shoot Through in Fast Switching VRM Applications,” Abril 2016. [Online]. Available: www.onsemi.com/pub/Collateral/AND9419-D.pdf. [Acesso em 07 Novembro 2018].

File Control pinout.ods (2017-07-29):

Standard connectors pins
Inverter pinout connection
Status signals |  |  | PWM arms A(1)/B(2) |  |  | PWM arms C(3)/N(4)
Ethernet connector 0 |  |  | Ethernet connector 1 |  |  | Ethernet connector 2
Pin | Signal | Direction | Pin | Signal | Direction | Pin | Signal | Direction
1 | 5V | (out) | 1 | PWM A(1) top | (in) | 1 | PWM C(3) top | (in) | TX+ | BI_DA+ | Green-White
2 | 5V | (out) | 2 | GND – PWM A(1) top |  | 2 | GND – PWM C(3) top |  | TX- | BI_DA- | Green
3 | General fault | (out) | 3 | PWM A(1) bottom | (in) | 3 | PWM C(3) bottom | (in) | RX+ | BI_DB+ | Orange-White
4 | Relay 1 | (in) | 4 | GND – PWM B(2) top |  | 4 | GND – PWM N(4) top |  |  | BI_DC+ | Blue
5 | Relay 2 | (in) | 5 | PWM B(2) top | (in) | 5 | PWM N(4) top | (in) |  | BIDC- | Blue-White
6 | Reset | (in) | 6 | GND – PWM A(1) bottom |  | 6 | GND – PWM C(3) bottom |  | RX- | BI_DB- | Orange
7 | Enable | (in) | 7 | PWM B(2) bottom | (in) | 7 | PWM N(4) bottom | (in) |  | BI_DD+ | Brown-White
8 | GND |  | 8 | GND – PWM B(2) bottom |  | 8 | GND – PWM N(4) bottom |  |  | BI_DD- | Brown
Extra connector
1 | +5V
2 | Fault arm A (1)
3 | Fault arm B (2)
4 | Fault arm C (3)
5 | Fault arm N (4)
6 | GND
7 | GND
The fault siggnals are active LOW and
HIGH IMPEDANCE in natural conditions.
Written by Hildo G Jr and Fellipe Garcia
Licensed under GNU GPL 3.0

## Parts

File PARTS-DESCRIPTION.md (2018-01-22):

This file describe the function of any part, schematic  sheet, of the project.
Any of this parts are divided by ROMs in the Altium project layout and some time replicated.

# Main power supplier
Sheet: MainPowerSupplier.SchDoc

Provides the positive voltage to the isolated power supplier, necessary do the gate drive, and the +5V to the logic circuits.

# Logic
Sheet: LogicCircuits.SchDoc

Provide:
1. The (if) necessary voltage level shift in the PWM / control signal (3.3V to 5V as HIGH LEVEL);
2. Error memory (of each arm) and board disable. By JUMPER selection, one error will disable all board, or even the relays, or only it arm;
3. Manual reset of the error (only if the board is not activated by the control connections);
4. PWM inputs, control of the relays, board enable and external reset connections in an RJ45 standard. Plus a extra connection HEADER errors identification;
5. Indication (LEDs) of the board status: power-on, activated, no-error or error in an specific phase;

# Dead-time + interlock
Sheet: DeadTimeDriver_Leg.SchDoc

Provide:
1. The minimum dead-time to any arm of the inverter (configurable). It is used the inherent trigger level of the gate input and a RC circuit plus DIODE to create a delay in only one transition;
2. The interlock (may be disable) between the HIGH SIDE and LOW SIDE group of transistors;

# Isolated power supplier
Sheet: GateDrivePowerSupply.SchDoc

Provide the isolated voltage to gate the transistors plus the +5V to the logic and protections circuits.

# Gate-drive + protections
Sheet: DriverAndProtection.SchDoc

Provide:
1. The fastest and stable way to drive TWO parallel transistors (MOSFETs) or single IGBTs on the max frequency and load specification of the project;
2. The isolation of the "drive/PWM" signal and the return of the error signal and a local disable of the gate circuit;
3. A error signal ACTIVE LOW by the protections and a HIGH SPEED memory, by two transistors;
4. FOUR protections to the transistors and gate circuit.

## Protection operation

Use a 2.5V reference voltage circuit and a comparator IC to provide the bellow protections:

1. **Low voltage gate driver**, included in the reference generator, it decrease the 2.5V reference voltage NET until any comparation threshold, in the case of low voltage in the isolated power supply;
2. **Over temperature** use a analog output temperature sensor close to one transistor terminal;
3. **Over voltage** compare the scaled voltage of the current conduction terminal of the group of transistors (DRAIN-SOURCE or EMITTER-COLLECTOR;
4. **Over current** use the same measure of the *over voltage* protection in a different instant and scale, only a little time after the transistor turned-on. The time of this comparison is controlled by the PWM signal that disable this when is LOW and allow this protection some nanoseconds after the PWM goes HIGH, changing the scaled voltage. When the PWM is LOW the scaled voltage is ZERO to prevent the wrong protection trigger.

# Gate drive circuit
Sheet: GateDriveCircuit.SchDoc

Provide:
1. Integration of the gate driver with the transistors;
2. Quick removal of the charges of the gate in the MOSFETs transistors;
3. The drive of TWO transistors in parallel without oscillation;
4. Attenuation of the overshoot in the turn-on stage.

# Power
Sheet: MainPower.SchDoc

Provide:
1. The main connections of the DC links and transistors to create the desired topology of study;
2. The capacitors connections and measurement points.

# Auxiliary
Sheet: Auxiliary.SchDoc

Provide TWO extra relays with them NO and NC connections.

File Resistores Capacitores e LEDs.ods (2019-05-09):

Item | Valor |  | Encapsulamento | Quantidade
Resistor | 0 | Ω | 805 | 100x
Resistor | 0,1 | Ω | 805 | 100x
Resistor | 0,22 | Ω | 805 | 100x
Resistor | 0,47 | Ω | 805 | 100x
Resistor | 1 | Ω | 805 | 100x
Resistor | 1,2 | Ω | 805 | 100x
Resistor | 1,5 | Ω | 805 | 100x
Resistor | 1,8 | Ω | 805 | 100x
Resistor | 2,2 | Ω | 805 | 100x
Resistor | 2,7 | Ω | 805 | 100x
Resistor | 3,3 | Ω | 805 | 100x
Resistor | 3,9 | Ω | 805 | 100x
Resistor | 4,7 | Ω | 805 | 100x
Resistor | 5,6 | Ω | 805 | 100x
Resistor | 6,8 | Ω | 805 | 100x
Resistor | 8,2 | Ω | 805 | 100x
Resistor | 9,1 | Ω | 805 | 100x
Resistor | 10 | Ω | 805 | 100x
Resistor | 12 | Ω | 805 | 100x
Resistor | 15 | Ω | 805 | 100x
Resistor | 18 | Ω | 805 | 100x
Resistor | 22 | Ω | 805 | 100x
Resistor | 27 | Ω | 805 | 100x
Resistor | 33 | Ω | 805 | 100x
Resistor | 39 | Ω | 805 | 100x
Resistor | 47 | Ω | 805 | 100x
Resistor | 56 | Ω | 805 | 100x
Resistor | 68 | Ω | 805 | 100x
Resistor | 82 | Ω | 805 | 100x
Resistor | 91 | Ω | 805 | 100x
Resistor | 100 | Ω | 805 | 100x
Resistor | 120 | Ω | 805 | 100x
Resistor | 150 | Ω | 805 | 100x
Resistor | 180 | Ω | 805 | 100x
Resistor | 220 | Ω | 805 | 100x
Resistor | 270 | Ω | 805 | 100x
Resistor | 330 | Ω | 805 | 100x
Resistor | 390 | Ω | 805 | 100x
Resistor | 470 | Ω | 805 | 100x
Resistor | 560 | Ω | 805 | 100x
Resistor | 680 | Ω | 805 | 100x
Resistor | 820 | Ω | 805 | 100x
Resistor | 910 | Ω | 805 | 100x
Resistor | 1 | kΩ | 805 | 100x
Resistor | 1,2 | kΩ | 805 | 100x
Resistor | 1,5 | kΩ | 805 | 100x
Resistor | 1,8 | kΩ | 805 | 100x
Resistor | 2,2 | kΩ | 805 | 100x
Resistor | 2,7 | kΩ | 805 | 100x
Resistor | 3,3 | kΩ | 805 | 100x
Resistor | 3,9 | kΩ | 805 | 100x
Resistor | 4,7 | kΩ | 805 | 100x
Resistor | 5,6 | kΩ | 805 | 100x
Resistor | 6,8 | kΩ | 805 | 100x
Resistor | 8,2 | kΩ | 805 | 100x
Resistor | 9,1 | kΩ | 805 | 100x
Resistor | 10 | kΩ | 805 | 100x
Resistor | 12 | kΩ | 805 | 100x
Resistor | 15 | kΩ | 805 | 100x
Resistor | 18 | kΩ | 805 | 100x
Resistor | 22 | kΩ | 805 | 100x
Resistor | 27 | kΩ | 805 | 100x
Resistor | 33 | kΩ | 805 | 100x
Resistor | 39 | kΩ | 805 | 100x
Resistor | 47 | kΩ | 805 | 100x
Resistor | 56 | kΩ | 805 | 100x
Resistor | 68 | kΩ | 805 | 100x
Resistor | 82 | kΩ | 805 | 100x
Resistor | 91 | kΩ | 805 | 100x
Resistor | 100 | kΩ | 805 | 100x
Resistor | 120 | kΩ | 805 | 100x
Resistor | 150 | kΩ | 805 | 100x
Resistor | 180 | kΩ | 805 | 100x
Resistor | 220 | kΩ | 805 | 100x
Resistor | 270 | kΩ | 805 | 100x
Resistor | 330 | kΩ | 805 | 100x
Resistor | 390 | kΩ | 805 | 100x
Resistor | 470 | kΩ | 805 | 100x
Resistor | 560 | kΩ | 805 | 100x
Resistor | 680 | kΩ | 805 | 100x
Resistor | 820 | kΩ | 805 | 100x
Resistor | 910 | kΩ | 805 | 100x
Resistor
Resistor | 1 | MΩ | 805 | 100x
Resistor | 1,2 | MΩ | 805 | 100x
Resistor | 1,5 | MΩ | 805 | 100x
Resistor | 1,8 | MΩ | 805 | 100x
Resistor | 2,2 | MΩ | 805 | 100x
Resistor | 2,7 | MΩ | 805 | 100x
Resistor | 3,3 | MΩ | 805 | 100x
Resistor | 3,9 | MΩ | 805 | 100x
Resistor | 4,7 | MΩ | 805 | 100x
Resistor | 5,6 | MΩ | 805 | 100x
Resistor | 6,8 | MΩ | 805 | 100x
Resistor | 8,2 | MΩ | 805 | 100x
Resistor | 9,1 | MΩ | 805 | 100x
Resistor | 10 | MΩ | 805 | 100x
Resistor | 15 | MΩ | 805 | 100x
Resistor | 22 | MΩ | 805 | 100x
Resistor | 0,1 | Ω | 1210 | 100x
Resistor | 0,22 | Ω | 1210 | 100x
Resistor | 0,47 | Ω | 1210 | 100x
Resistor | 1 | Ω | 1210 | 100x
Resistor | 1,2 | Ω | 1210 | 100x
Resistor | 1,5 | Ω | 1210 | 100x
Resistor | 2,2 | Ω | 1210 | 100x
Resistor | 4,7 | Ω | 1210 | 100x
Resistor | 10 | Ω | 1210 | 100x
Resistor | 22 | Ω | 1210 | 100x
Resistor | 47 | Ω | 1210 | 100x
 |  |  |  | 100x
Resistor | 0,1 | kΩ | 1210 | 100x
Resistor | 0,22 | kΩ | 1210 | 100x
Resistor | 0,47 | kΩ | 1210 | 100x
Resistor | 1 | kΩ | 1210 | 100x
Resistor | 2,2 | kΩ | 1210 | 100x
Resistor | 4,7 | kΩ | 1210 | 100x
Resistor | 10 | kΩ | 1210 | 100x
Resistor | 22 | kΩ | 1210 | 100x
Resistor | 47 | kΩ | 1210 | 100x
Resistor | 0,1 | MΩ | 1210 | 100x
Resistor | 0,22 | MΩ | 1210 | 100x
Resistor | 0,47 | MΩ | 1210 | 100x
Resistor | 1 | MΩ | 1210 | 100x
Resistor | 2,2 | MΩ | 1210 | 100x
Resistor | 4,7 | MΩ | 1210 | 100x
Resistor | 10 | MΩ | 1210 | 100x
Resistor | 0 | Ω | 1210 | 100x
Item | Valor |  | Encapsulamento | Quantidade | Tensão
Capacitor | 1 | pF | 805 | 100x | 50V
Capacitor | 2,2 | pF | 805 | 100x | 50V
Capacitor | 3,3 | pF | 805 | 100x | 50V
Capacitor | 4,7 | pF | 805 | 100x | 50V
Capacitor | 6,8 | pF | 805 | 100x | 50V
Capacitor |  |  | 805 | 100x | 50V
Capacitor | 10 | pF | 805 | 100x | 50V
Capacitor | 22 | pF | 805 | 100x | 50V
Capacitor | 33 | pF | 805 | 100x | 50V
Capacitor | 47 | pF | 805 | 100x | 50V
Capacitor | 68 | pF | 805 | 100x | 50V
Capacitor | 100 | pF | 805 | 100x | 50V
Capacitor | 220 | pF | 805 | 100x | 50V
Capacitor | 330 | pF | 805 | 100x | 50V
Capacitor | 470 | pF | 805 | 100x | 50V
Capacitor | 680 | pF | 805 | 100x | 50V
Capacitor | 1 | nF | 805 | 100x | 50V
Capacitor | 2,2 | nF | 805 | 100x | 50V
Capacitor | 3,3 | nF | 805 | 100x | 50V
Capacitor | 4,7 | nF | 805 | 100x | 50V
Capacitor | 6,8 | nF | 805 | 100x | 50V
Capacitor | 10 | nF | 805 | 100x | 50V
Capacitor | 22 | nF | 805 | 100x | 50V
Capacitor | 33 | nF | 805 | 100x | 50V
Capacitor | 47 | nF | 805 | 100x | 50V
Capacitor | 68 | nF | 805 | 100x | 50V
 |  |  | 805 | 100x | 50V
Capacitor | 100 | nF | 805 | 100x | 50V
Capacitor | 220 | nF | 805 | 100x | 50V
Capacitor | 330 | nF | 805 | 100x | 50V
Capacitor | 470 | nF | 805 | 100x | 50V
Capacitor | 680 | nF | 805 | 100x | 50V
Capacitor |  |  | 805 | 100x | 50V
Capacitor | 1 | uF | 805 | 100x | 50V
Capacitor | 100 | nF | 1210 | 500x | 50V
Capacitor | 220 | nF | 1210 | 100x | 50V
Capacitor | 470 | nF | 1210 | 100x | 50V
 |  |  | 1210 | 100x | 50V
Capacitor | 1 | uF | 1210 | 100x | 50V
Capacitor | 2,2 | uF | 1210 | 100x | 50V
Capacitor | 4,7 | uF | 1210 | 100x | 50V
Capacitor | 2,2 | uF | 805 | 50x | 16V
Capacitor | 4,7 | uF | 805 | 50x | 16V
Capacitor | 10 | uF | 805 | 50x | 16V
Capacitor | 10 | uF | 1210 | 50x | 16V
Capacitor | 15 | uF | 1210 | 50x | 16V
Capacitor | 22 | uF | 1210 | 50x | 16V
Item | Valor |  | Encapsulamento | Quantidade
Verde |  |  | 805 | 100x
Vermelho |  |  | 805 | 100x
Amarelo |  |  | 805 | 100x

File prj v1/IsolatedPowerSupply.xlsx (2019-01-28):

Prj: | IsolatedPowerSupply.xml |  |  |  |  | Board Qty: | 1
Co.: |  |  |  |  |  | Unit Cost: | $5.19
Prj date: | 2018-01-10 18:14:10 (file) |  |  |  |  | Total Cost: | $5.19 |  |  |  | $7.74 | 15 of 16 parts found |  |  |  | $3.48 | 9 of 16 parts found |  |  |  | $0.62 | 1 of 16 parts found |  |  |  | $3.06 | 10 of 16 parts found |  |  |  | $0.00 | 0 |  |  |  | $0.71 | 6 of 16 parts found
$ date: | 2018-06-29 11:10:16
Global Part Info |  |  |  |  |  |  |  | Digi-Key |  |  |  |  | Farnell |  |  |  |  | Mouser |  |  |  |  | Newark |  |  |  |  | Rs Components |  |  |  |  | Tme
Refs | Value | Desc | Footprint | Manf# | Qty | Unit$ | Ext$ | Avail | Purch | Unit$ | Ext$ | Cat# | Avail | Purch | Unit$ | Ext$ | Cat# | Avail | Purch | Unit$ | Ext$ | Cat# | Avail | Purch | Unit$ | Ext$ | Cat# | Avail | Purch | Unit$ | Ext$ | Cat# | Avail | Purch | Unit$ | Ext$ | Cat#
C19 | 2.2uF | Capacitor nao polarizado | 0805_W | 08053C225KAT2A | 1 | $0.07 | $0.07 | NonStk |  | $0.35 | $0.35 | 478-5719-1-ND (https://www.digikey.com/product-detail/en/avx-corporation/08053C225KAT2A/478-5719-1-ND/2136327) | NonStk |  | $0.10 | $0.10 | 2280956 (http://it.farnell.com/Search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) |  |  |  |  |  | NonStk |  | $0.07 | $0.07 | 10R5975 (http://www.newark.com/avx/08053c225kat2a/ceramic-capacitor-2-2uf-25v-x7r/dp/10R5975?st=08053C225KAT2A) |  |  |  |  |  | NonStk |  | $0.28 | $0.28 | 08053C225KAT2A (https://www.tme.eu/en/details/08053c225kat2a/0805-mlcc-smd-capacitors/avx/)
C25 | 1nF | Capacitor | 0805_W | 08053C102KAT2A | 1 | $0.01 | $0.01 | NonStk |  | $0.05 | $0.05 | 08053C102KAT2A-ND (https://www.digikey.com/products/en?keywords=08053C102KAT2A) | 5185 |  | $0.01 | $0.01 | 1856454 (http://it.farnell.com/multicomp/mcsh21b102k250ct/condensatore-mlcc-x7r-1nf-25v/dp/1856454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) |  |  |  |  |  | NonStk |  | $0.04 | $0.04 | 25H6309 (http://www.newark.com/webapp/wcs/stores/servlet/Search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) |  |  |  |  |  | NonStk |  | $0.01 | $0.01 | 08053C102KAT2A (https://www.tme.eu/en/details/08053c102kat2a/0805-mlcc-smd-capacitors/avx/)
C20-C24,Cin2 | 100nF | C20-C22: Capacitor nao polarizado C23,C24,Cin2: Capacitor | 0805_W | 08053C104KAT2A | 6 | $0.02 | $0.14 | NonStk |  | $0.20 | $1.20 | 478-3755-1-ND (https://www.digikey.com/product-detail/en/avx-corporation/08053C104KAT2A/478-3755-1-ND/1116453) | NonStk |  | $0.09 | $0.55 | 1740665 (http://it.farnell.com/avx/08053c104kat2a/condensatore-mlcc-x7r-100nf-25v/dp/1740665?st=08053C104KAT2A) |  |  |  |  |  | NonStk |  | $0.02 | $0.14 | 84C9177 (http://www.newark.com/avx/08053c104kat2a/ceramic-capacitor-0-1uf-25v-x7r/dp/84C9177?st=08053C104KAT2A) | NonStk |  |  |  | 390-990 (http://it.rs-online.com/web/c/?searchTerm=08053C104KAT2A)
Cin1 | 1uF | Capacitor | 0805_W | 08053C105KAT2A | 1 | $0.04 | $0.04 | NonStk |  | $0.28 | $0.28 | 478-5030-1-ND (https://www.digikey.com/product-detail/en/avx-corporation/08053C105KAT2A/478-5030-1-ND/1888241) | NonStk |  | $0.34 | $0.34 | 1658877 (http://it.farnell.com/avx/08053c105kat2a/condensatore-mlcc-x7r-1uf-25v/dp/1658877?st=08053C105KAT2A) |  |  |  |  |  | NonStk |  | $0.04 | $0.04 | 70K6963 (http://www.newark.com/avx/08053c105kat2a/ceramic-capacitor-1uf-25v-x7r/dp/70K6963?st=08053C105KAT2A) |  |  |  |  |  | 500 |  | $0.22 | $0.22 | 08053C105KAT2A (https://www.tme.eu/en/details/08053c105kat2a/0805-mlcc-smd-capacitors/avx/)
D9,D10 | BAT46Z | Schottky Diode | SOD-123 | BAT46ZFILM | 2 | $0.08 | $0.17 | 42988 |  | $0.36 | $0.72 | 497-5559-1-ND (https://www.digikey.com/product-detail/en/stmicroelectronics/BAT46ZFILM/497-5559-1-ND/1207051) | 6982 |  | $0.31 | $0.63 | 2341640 (http://it.farnell.com/stmicroelectronics/bat46zfilm/diodo-schottky-0-15a-100v-sod/dp/2341640?st=BAT46ZFILM) |  |  |  |  |  | 554 |  | $0.35 | $0.70 | 05X9522 (http://www.newark.com/stmicroelectronics/bat46zfilm/small-signal-diode-100-v-150-ma/dp/05X9522?st=BAT46ZFILM) |  |  |  |  |  | 6366 |  | $0.08 | $0.17 | BAT46ZFILM (https://www.tme.eu/en/details/bat46zfilm/smd-schottky-diodes/st-microelectronics/)
IN_1,OUT_1,OUT_2 |  | Header | Header2 | 1935161 | 3 | $0.38 | $1.13 | 37794 |  | $0.41 | $1.23 | 277-1667-ND (https://www.digikey.com/products/en?keywords=1935161) | 2048 |  | $0.38 | $1.13 | 1793674 (http://it.farnell.com/Search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) |  |  |  |  |  | 61 |  | $0.43 | $1.29 | 70R0063 (http://www.newark.com/webapp/wcs/stores/servlet/Search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) | NonStk |  |  |  | 548-7238 (http://it.rs-online.com/web/c/?searchTerm=1935161)
Q3 | BC857B | PNP General-purpose Transistor | SOT-23-TT3_N | BC857BLT1G | 1 | $0.01 | $0.01 | 1973 |  | $0.12 | $0.12 | BC857BLT1GOSCT-ND (https://www.digikey.com/product-detail/en/on-semiconductor/BC857BLT1G/BC857BLT1GOSCT-ND/917843) | 7260 |  | $0.04 | $0.04 | 1459044 (http://it.farnell.com/on-semiconductor/bc857blt1g/transistor-pnp-sot-23/dp/1459044?st=BC857BLT1G) |  |  |  |  |  | 24000 |  | $0.02 | $0.02 | 85W3125 (http://www.newark.com/on-semiconductor/bc857blt1g/bipolar-transistor-pnp-45v-sot/dp/85W3125?st=BC857BLT1G) |  |  |  |  |  | 33000 |  | $0.01 | $0.01 | BC857BLT1G (https://www.tme.eu/en/details/bc857blt1g/pnp-smd-transistors/on-semiconductor/)
Q4 | BC847B | NPN General-purpose Transistor | SOT-23-TT3_N | BC847BLT1G | 1 | $0.03 | $0.03 | 191254 |  | $0.12 | $0.12 | BC847BLT1GOSCT-ND (https://www.digikey.com/product-detail/en/on-semiconductor/BC847BLT1G/BC847BLT1GOSCT-ND/917834) | 6000 |  | $0.04 | $0.04 | 2317816 (http://it.farnell.com/on-semiconductor/bc847blt1g/transistor-npn-45v-100ma-sot-23/dp/2317816?st=BC847BLT1G) |  |  |  |  |  | 48834 |  | $0.12 | $0.12 | 88H4566 (http://www.newark.com/on-semiconductor/bc847blt1g/bipolar-transistor-npn-45v-sot/dp/88H4566?st=BC847BLT1G) | NonStk |  |  |  | 545-2759 (http://it.rs-online.com/web/c/?searchTerm=BC847BLT1G) | 23266 |  | $0.03 | $0.03 | BC847BLT1G (https://www.tme.eu/en/details/bc847blt1g/npn-smd-transistors/on-semiconductor/)
R26 | 12K | Resistor | 0805_W | RMCF0805JT12K0 | 1 | $0.01 | $0.01 | 29355 |  | $0.10 | $0.10 | RMCF0805JT12K0CT-ND (https://www.digikey.com/product-detail/en/stackpole-electronics-inc/RMCF0805JT12K0/RMCF0805JT12K0CT-ND/5049816) |  |  |  |  |  |  |  |  |  |  | NonStk |  | $0.01 | $0.01 | 65J1424 (http://www.newark.com/vishay/crcw080512k0jntc/resistor-metal-glaze-12kohms-150wv/dp/65J1424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)
R27 | 3.3k | Resistor | 0805_W | RMCF0805JT3K30 | 1 | $0.10 | $0.10 | 7696 |  | $0.10 | $0.10 | RMCF0805JT3K30CT-ND (https://www.digikey.com/product-detail/en/stackpole-electronics-inc/RMCF0805JT3K30/RMCF0805JT3K30CT-ND/1942567)
R28,R29 | 1R5 | Resistor | 0805_W | RMCF0805JT1R50 | 2 | $0.10 | $0.20 | 3420 |  | $0.10 | $0.20 | RMCF0805JT1R50CT-ND (https://www.digikey.com/product-detail/en/stackpole-electronics-inc/RMCF0805JT1R50/RMCF0805JT1R50CT-ND/4425249)
R30 | not used | Resistor | 0805_W |  | 1 | $0.00 | $0.00
R31 | 4.7k | Resistor | 0805_W | RMCF0805JT4K70 | 1 | $0.10 | $0.10 | 1062 |  | $0.10 | $0.10 | RMCF0805JT4K70CT-ND (https://www.digikey.com/product-detail/en/stackpole-electronics-inc/RMCF0805JT4K70/RMCF0805JT4K70CT-ND/1942570)
T1 | Wurth 1:2 |  | Trafo | 760390015 | 1 | $1.90 | $1.90 | 58461 |  | $1.90 | $1.90 | 732-4459-1-ND (https://www.digikey.com/product-detail/en/wurth-electronics-midcom/760390015/732-4459-1-ND/3831268)
U7 | TL494 | Pulse-Width-Modulation Control Circuit | SOIC16_M | TL494IDR | 1 | $0.65 | $0.65 | 6966 |  | $0.65 | $0.65 | 296-24387-1-ND (https://www.digikey.com/product-detail/en/texas-instruments/TL494IDR/296-24387-1-ND/2051878)
U8 | LM7805 |  | LM78XX | UA78M05CDCY | 1 | $0.62 | $0.62 | 51034 |  | $0.62 | $0.62 | 296-27138-5-ND (https://www.digikey.com/product-detail/en/texas-instruments/UA78M05CDCY/296-27138-5-ND/1910303) | 5862 |  | $0.63 | $0.63 | 2296030 (http://it.farnell.com/texas-instruments/ua78m05cdcy/v-reg-0-5a-5v-5-4sot223/dp/2296030?st=UA78M05CDCY) | 2570 |  | $0.62 | $0.62 | 595-UA78M05CDCY (https://www.mouser.com/ProductDetail/Texas-Instruments/UA78M05CDCY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) | 1310 |  | $0.62 | $0.62 | 77C1885 (http://www.newark.com/texas-instruments/ua78m05cdcy/linear-voltage-regulator-5v-sot/dp/77C1885?st=UA78M05CDCY)
Distributors scraped by KiCost® v.0.1.46 |  |  |  |  |  |  |  |  | 0 |  |  |  |  | 0 |  |  |  |  | 0 |  |  |  |  | 0 |  |  |  |  | 0 |  |  |  |  | 0

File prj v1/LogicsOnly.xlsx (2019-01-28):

Prj: | LogicsOnly.xml |  |  |  | Board Qty: | 1
Co.: |  |  |  |  | Unit Cost: | $27.91
Prj date: | 2018-01-10 18:14:30 (file) |  |  |  | Total Cost: | $27.91 |  |  |  | $34.40 | 30 of 53 parts found |  |  |  | $57.13 | 11 of 53 parts found |  |  |  | $0.00 | 0 |  |  |  | $13.51 | 11 of 53 parts found |  |  |  | $10.87 | 12 of 53 parts found |  |  |  | $3.13 | 7 of 53 parts found
$ date: | 2018-06-29 11:18:03
Global Part Info |  |  |  |  |  |  | Digi-Key |  |  |  |  | Farnell |  |  |  |  | Mouser |  |  |  |  | Newark |  |  |  |  | Rs Components |  |  |  |  | Tme
Refs | Value | Footprint | Manf# | Qty | Unit$ | Ext$ | Avail | Purch | Unit$ | Ext$ | Cat# | Avail | Purch | Unit$ | Ext$ | Cat# | Avail | Purch | Unit$ | Ext$ | Cat# | Avail | Purch | Unit$ | Ext$ | Cat# | Avail | Purch | Unit$ | Ext$ | Cat# | Avail | Purch | Unit$ | Ext$ | Cat#
C1,C2 | not used | 0805_W |  | 2 | $0.00 | $0.00
C35,C36 | 100nF | 0805_W |  | 2 | $0.00 | $0.00
C10-C12 | [NoValue] | 0805_W |  | 3 | $0.00 | $0.00
C37-C40 | 100nF | 0805_W | C0805C104K8RACTU | 4 | $0.11 | $0.45 | NonStk |  | $0.19 | $0.76 | 399-7999-1-ND (https://www.digikey.com/product-detail/en/kemet/C0805C104K8RACTU/399-7999-1-ND/3471722) | NonStk |  | $0.11 | $0.45 | 2773207RL (http://it.farnell.com/kemet/c0805c104k8ractu/condensatore-mlcc-x7r-0-1uf-10v/dp/2773207RL?st=C0805C104K8RACTU) |  |  |  |  |  | 3242 |  | $0.39 | $1.56 | 07X0869 (http://www.newark.com/kemet/c0805c104k8ractu/mlcc-capacitor-0-1uf-10v-x7r-10/dp/07X0869?st=C0805C104K8RACTU)
C4.DTA0,C3.DTD0,C4.DTC0,C42,C3.DTA0,Css1,C4.DTB0,C3.DTC0,C3.DTB0,C4.DTD0,Cbst1 | 100nF | 0805_W | 08053C104KAT2A | 11 | $0.02 | $0.26 | NonStk |  | $0.14 | $1.58 | 478-3755-1-ND (https://www.digikey.com/product-detail/en/avx-corporation/08053C104KAT2A/478-3755-1-ND/1116453) | NonStk |  | $0.09 | $1.01 | 1740665 (http://it.farnell.com/avx/08053c104kat2a/condensatore-mlcc-x7r-100nf-25v/dp/1740665?st=08053C104KAT2A) |  |  |  |  |  | NonStk |  | $0.02 | $0.26 | 84C9177 (http://www.newark.com/avx/08053c104kat2a/ceramic-capacitor-0-1uf-25v-x7r/dp/84C9177?st=08053C104KAT2A) | 1950 |  | $0.21 | $2.33 | 390-990 (http://it.rs-online.com/web/c/?searchTerm=08053C104KAT2A)
C6.DTB0,C5.DTB0,C6.DTA0,C6.DTC0,C7.DTA0,C5.DTC0,C7.DTB0,C5.DTA0,C7.DTD0,C7.DTC0,C5.DTD0,C6.DTD0 | 10nF | 0805_W |  | 12 | $0.00 | $0.00
Cin3 | 3.3uF | 1210_W |  | 1 | $0.00 | $0.00
Cinx1 | 1uF | 0805_W |  | 1 | $0.00 | $0.00
Cout1 | 10uF | 0805_W | C0805C106K8PACTU | 1 | $0.08 | $0.08 | NonStk |  | $0.15 | $0.15 | 399-4925-1-ND (https://www.digikey.com/product-detail/en/kemet/C0805C106K8PACTU/399-4925-1-ND/1090920) |  |  |  |  |  |  |  |  |  |  |  |  |  |  |  | 600 |  | $0.08 | $0.08 | 802-9850 (http://it.rs-online.com/web/p/condensatori-ceramici-multistrato/8029850/) | NonStk |  | $0.17 | $0.17 | C0805C106K8PAC (https://www.tme.eu/en/details/c0805c106k8pac/0805-mlcc-smd-capacitors/kemet/c0805c106k8pactu/)
D1,D3,D32,D445 | Green LED | LED_0805 | SML-LXR85GC-TR | 4 | $0.47 | $1.88 | 84199 |  | $0.47 | $1.88 | 67-1557-1-ND (https://www.digikey.com/product-detail/en/lumex-opto-components-inc/SML-LXR85GC-TR/67-1557-1-ND/304376)
D2,D4 | 1N4148 | SOD-123 | 1N4148W-TP | 2 | $0.14 | $0.28 | 514861 |  | $0.14 | $0.28 | 1N4148WTPMSCT-ND (https://www.digikey.com/product-detail/en/micro-commercial-co/1N4148W-TP/1N4148WTPMSCT-ND/717311) | NonStk |  | $0.21 | $0.43 | 1924519 (http://it.farnell.com/micro-commercial-components/1n4148w-tp/switching-diode-150ma-100v-sod123/dp/1924519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) |  |  |  |  |  | NonStk |  | $0.18 | $0.36 | 51T5044 (http://www.newark.com/micro-commercial-components/1n4148w-tp/switching-diode-150ma-100v-sod123/dp/51T5044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)
D33 | B240A | SOD-123 | B360A-13-F | 1 | $0.22 | $0.22 | 29499 |  | $0.48 | $0.48 | B360A-FDICT-ND (https://www.digikey.com/product-detail/en/diodes-incorporated/B360A-13-F/B360A-FDICT-ND/724980) | 31153 |  | $0.40 | $0.40 | 1858600 (http://it.farnell.com/diodes-inc/b360a-13-f/diodo-schottky-60v-3a-sma/dp/1858600?st=B360A-13-F) |  |  |  |  |  | 28441 |  | $0.44 | $0.44 | 23T4615 (http://www.newark.com/diodes-inc/b360a-13-f/diode-rectifier-schottky-60v-3a/dp/23T4615?st=B360A-13-F) | 270 |  | $0.37 | $0.37 | 738-4796 (http://it.rs-online.com/web/p/diodi-rettificatori-e-schottky/7384796/) | 4693 |  | $0.22 | $0.22 | B360A-13-F (https://www.tme.eu/en/details/b360a-13-f/smd-schottky-diodes/diodes-incorporated/)
D9 | Yellow LED | LED_0805 | SML-LXR85YC-TR | 1 | $0.43 | $0.43 | 5806 |  | $0.43 | $0.43 | 67-1558-1-ND (https://www.digikey.com/product-detail/en/lumex-opto-components-inc/SML-LXR85YC-TR/67-1558-1-ND/304378)
D26-D29 | Red LED | LED_0805 | SML-LXR85IC-TR | 4 | $0.54 | $2.16 | 5357 |  | $0.54 | $2.16 | 67-1556-1-ND (https://www.digikey.com/product-detail/en/lumex-opto-components-inc/SML-LXR85IC-TR/67-1556-1-ND/304374)
D8.DTD0,D7.DTA0,D5.DTD0,D5.DTA0,D6.DTD0,D6.DTB0,D6.DTA0,D8.DTC0,D8.DTA0,D5.DTC0,D7.DTC0,D6.DTC0,D7.DTD0,D21-D25,D7.DTB0,D8.DTB0,D5.DTB0 | BAT46Z | SOD-123 | BAT46ZFILM | 21 | $0.08 | $1.74 | 42988 |  | $0.27 | $5.59 | 497-5559-1-ND (https://www.digikey.com/product-detail/en/stmicroelectronics/BAT46ZFILM/497-5559-1-ND/1207051) | 6982 |  | $0.31 | $6.57 | 2341640 (http://it.farnell.com/stmicroelectronics/bat46zfilm/diodo-schottky-0-15a-100v-sod/dp/2341640?st=BAT46ZFILM) |  |  |  |  |  | 554 |  | $0.22 | $4.68 | 05X9522 (http://www.newark.com/stmicroelectronics/bat46zfilm/small-signal-diode-100-v-150-ma/dp/05X9522?st=BAT46ZFILM) | 1600 |  | $0.11 | $2.36 | 714-6850 (http://it.rs-online.com/web/p/diodi-rettificatori-e-schottky/7146850/) | 6366 |  | $0.08 | $1.74 | BAT46ZFILM (https://www.tme.eu/en/details/bat46zfilm/smd-schottky-diodes/st-microelectronics/)
Faults0 | Header 7 |  |  | 1 | $0.00 | $0.00
Fix1#1,Fix2#1,Fix3#1,Fix4#1 | Pin - p1/2 | Pino | 908-100 | 4 | $0.10 | $0.40 |  |  |  |  |  | NonStk |  | $0.10 | $0.40 | 2751474 (http://it.farnell.com/Search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) |  |  |  |  |  | 2579 |  | $0.39 | $1.56 | 96B5833 (http://www.newark.com/webapp/wcs/stores/servlet/Search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)
Fix1#2,Fix2#2,Fix3#2,Fix4#2 | Pin - p2/2 | Pino | RM2X12MM 2701 | 4 | $0.75 | $3.00 | 892 |  | $0.75 | $3.00 | 335-1151-ND (https://www.digikey.com/products/en?keywords=RM2X12MM+2701)
INV_CONTROL0,PWM_CN0,PWM_AB0 | RJ-45 | RJ-45 | A-2004-2-4-LPS-N-R | 3 | $1.05 | $3.15 | 25023 |  | $1.05 | $3.15 | AE10387-ND (https://www.digikey.com/products/en?keywords=A-2004-2-4-LPS-N-R)
JP5 | Header 2 | HDR1X2 |  | 1 | $0.00 | $0.00
JP7.DTA0,JP7.DTB0,JP6.DTC0,JP7.DTD0,JP1.DTC0,JP6.DTD0,JP4.DTB0,JP4.DTA0,JP7.DTC0,JP1.DTD0,JP4.DTC0,JP3.DTB0,JP6.DTB0,JP4.DTD0,JP3.DTA0,JP2.DTA0,JP2.DTB0,JP3.DTC0,JP3.DTD0,JP1.DTB0,JP2.DTC0,JP6.DTA0,JP2.DTD0,JP1.DTA0 | solder jumper | Jumper |  | 24 | $0.00 | $0.00
K1,K2 | Relay 9V coil - 10A | Relay - SPDT | G5LE-14-DC9 | 2 | $1.44 | $2.88 | 7041 |  | $1.44 | $2.88 | Z3112-ND (https://www.digikey.com/products/en?keywords=G5LE-14-DC9) |  |  |  |  |  |  |  |  |  |  |  |  |  |  |  | 14 |  |  |  | 807-4065 (http://it.rs-online.com/web/c/?searchTerm=G5LE-14-DC9)
L0 | 8.2uH | SRN8040T - Inductor | SRN8040-8R2Y | 1 | $0.44 | $0.44 | 9027 |  | $0.66 | $0.66 | SRN8040-8R2YCT-ND (https://www.digikey.com/product-detail/en/bourns-inc/SRN8040-8R2Y/SRN8040-8R2YCT-ND/2756179) |  |  |  |  |  |  |  |  |  |  |  |  |  |  |  | 20 |  | $0.44 | $0.44 | 743-5172 (http://it.rs-online.com/web/p/induttori-avvolti-smd/7435172/)
Manual Reset0 | Tactile SPST-NO | Tactile SPST-NO | FSM4JH | 1 | $0.10 | $0.10 | 66440 |  | $0.10 | $0.10 | 450-1650-ND (https://www.digikey.com/product-detail/en/te-connectivity-alcoswitch-switches/1825910-6/450-1650-ND/1632536)
P3,P4 | Bornier | KK-3_G | 1935174 | 2 | $0.54 | $1.08 |  |  |  |  |  | 200 |  | $22.96 | $45.92 | 1935174 (http://it.farnell.com/samtec/ffsd-17-s-19-00-01-n/conduttore-1-27mm-idc-19in-34/dp/1935174?st=1935174) |  |  |  |  |  | 309 |  | $0.54 | $1.08 | 70R0065 (http://www.newark.com/webapp/wcs/stores/servlet/Search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) | 70 |  | $0.70 | $1.41 | 548-7244 (http://it.rs-online.com/web/c/?searchTerm=1935174)
P3000 | Header 5X2 | HDR2X5 |  | 1 | $0.00 | $0.00
P7 | Header 3 | HDR1X3 |  | 1 | $0.00 | $0.00
Q1,Q2 | BC847 | SOT-23-TT3_L | BC847BLT1G | 2 | $0.02 | $0.03 | 191254 |  | $0.12 | $0.24 | BC847BLT1GOSCT-ND (https://www.digikey.com/product-detail/en/on-semiconductor/BC847BLT1G/BC847BLT1GOSCT-ND/917834) |  |  |  |  |  |  |  |  |  |  |  |  |  |  |  | NonStk |  | $0.02 | $0.03 | 545-2759 (http://it.rs-online.com/web/c/?searchTerm=BC847BLT1G) | 23266 |  | $0.03 | $0.06 | BC847BLT1G (https://www.tme.eu/en/details/bc847blt1g/npn-smd-transistors/on-semiconductor/)
Q7 | BC847 | SOT-23-TT3_N | BC847BLT1G | 1 | $0.02 | $0.02 |  |  |  |  |  |  |  |  |  |  |  |  |  |  |  |  |  |  |  |  | NonStk |  | $0.02 | $0.02 | 545-2759 (http://it.rs-online.com/web/c/?searchTerm=BC847BLT1G) | 23266 |  | $0.03 | $0.03 | BC847BLT1G (https://www.tme.eu/en/details/bc847blt1g/npn-smd-transistors/on-semiconductor/)
R1 | 680R | 0805_W | RMCF0805JT680R | 1 | $0.10 | $0.10 | 354085 |  | $0.10 | $0.10 | RMCF0805JT680RCT-ND (https://www.digikey.com/product-detail/en/stackpole-electronics-inc/RMCF0805JT680R/RMCF0805JT680RCT-ND/1942554)
R2,R4 | 4k7 | 0805_W | RMCF0805JT4K70 | 2 | $0.10 | $0.20 | 1062 |  | $0.10 | $0.20 | RMCF0805JT4K70CT-ND (https://www.digikey.com/product-detail/en/stackpole-electronics-inc/RMCF0805JT4K70/RMCF0805JT4K70CT-ND/1942570)
R3 | 220 | 0805_W | RMCF0805JT680R | 1 | $0.10 | $0.10 | 354085 |  | $0.10 | $0.10 | RMCF0805JT680RCT-ND (https://www.digikey.com/product-detail/en/stackpole-electronics-inc/RMCF0805JT680R/RMCF0805JT680RCT-ND/1942554)
R36,R38,R39,R74-R78,R80-R82 | 47R | 0805_W | RMCF0805JT47R0 | 11 | $0.02 | $0.19 | 171810 |  | $0.02 | $0.19 | RMCF0805JT47R0CT-ND (https://www.digikey.com/product-detail/en/stackpole-electronics-inc/RMCF0805JT47R0/RMCF0805JT47R0CT-ND/1942535) | 1249 |  | $0.03 | $0.30 | 1514868 (http://it.farnell.com/vishay/crcw080547r0jnea/res-thick-film-47r-5-0-125w-0805/dp/1514868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) |  |  |  |  |  | 1249 |  | $0.11 | $1.21 | 59M6915 (http://www.newark.com/vishay/crcw080547r0jnea/res-thick-film-47r-5-0-125w-0805/dp/59M6915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)
R48,R50,R64-R67,R72 | 1k | 0805_W | RMCF0805JT1K00 | 7 | $0.10 | $0.70 | 993055 |  | $0.10 | $0.70 | RMCF0805JT1K00CT-ND (https://www.digikey.com/product-detail/en/stackpole-electronics-inc/RMCF0805JT1K00/RMCF0805JT1K00CT-ND/1942557)
R49 | 100k | 0805_W |  | 1 | $0.00 | $0.00
R5,R12,R18-R26,R52-R63,R68-R71 | 47k | 0805_W | RMCF0805JT47K0 | 27 | $0.02 | $0.46 | 4595 |  | $0.02 | $0.46 | RMCF0805JT47K0CT-ND (https://www.digikey.com/product-detail/en/stackpole-electronics-inc/RMCF0805JT47K0/RMCF0805JT47K0CT-ND/1942588) | NonStk |  | $0.02 | $0.67 | 1514867 (http://it.farnell.com/Search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) |  |  |  |  |  | NonStk |  | $0.05 | $1.43 | 59M6914 (http://www.newark.com/vishay/crcw080547k0jnea/res-thick-film-47k-5-0-125w-0805/dp/59M6914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)
R51 | 4.7k | 0805_W | RMCF0805JT4K70 | 1 | $0.10 | $0.10 | 1062 |  | $0.10 | $0.10 | RMCF0805JT4K70CT-ND (https://www.digikey.com/product-detail/en/stackpole-electronics-inc/RMCF0805JT4K70/RMCF0805JT4K70CT-ND/1942570)
R73 | 330R | 0805_W | RMCF0805JT330R | 1 | $0.10 | $0.10 | 189867 |  | $0.10 | $0.10 | RMCF0805JT330RCT-ND (https://www.digikey.com/product-detail/en/stackpole-electronics-inc/RMCF0805JT330R/RMCF0805JT330RCT-ND/1942547)
R79 |  | 0805_W | 47R | 1 | $0.00 | $0.00
R7.DTB0,R6.DTB0,Rfb2,R13.DTD0,R13.DTC0,R7.DTA0,R16.DTA0,R15.DTB0,R10.DTA0,R9.DTC0,R10.DTC0,R13.DTB0,R17.DTB0,R14.DTA0,R7.DTC0,R8.DTC0,R14.DTB0,R6.DTA0,R6.DTC0,R17.DTA0,R11.DTC0,R14.DTD0,R16.DTB0,R17.DTC0,R15.DTC0,R15.DTD0,R9.DTB0,R8.DTA0,R17.DTD0,R11.DTB0,R16.DTC0,R8.DTD0,R10.DTB0,R6.DTD0,R7.DTD0,R13.DTA0,R16.DTD0,R8.DTB0,R11.DTA0,R10.DTD0,R9.DTA0,R11.DTD0,R14.DTC0,R9.DTD0,R15.DTA0 | 10k | 0805_W |  | 45 | $0.00 | $0.00
Rfb1 | 21.5k | 0805_W |  | 1 | $0.00 | $0.00
Rsns1 | 50m | 0805_W |  | 1 | $0.00 | $0.00
Rt1 | 180k | 0805_W |  | 1 | $0.00 | $0.00
SUPPLY0 | Bornier | 3 Pin Borner | 1935174 | 1 | $0.70 | $0.70 |  |  |  |  |  |  |  |  |  |  |  |  |  |  |  |  |  |  |  |  | 70 |  | $0.70 | $0.70 | 548-7244 (http://it.rs-online.com/web/c/?searchTerm=1935174)
Signals_1-Signals_4 | Header 5 | HDR1X5 |  | 4 | $0.00 | $0.00
U1 | LM25011MYX | 10MSOP | LM25011MYX/NOPB | 1 | $2.89 | $2.89 | 22012 |  | $2.89 | $2.89 | LM25011MY/NOPBCT-ND (https://www.digikey.com/product-detail/en/texas-instruments/LM25011MY-NOPB/LM25011MY-NOPBCT-ND/2080169)
U10 | SN74LS32 | SO14-Wide | SN74LS32NSR | 1 | $0.63 | $0.63 | 2050 |  | $0.63 | $0.63 | 296-3697-1-ND (https://www.digikey.com/product-detail/en/texas-instruments/SN74LS32NSR/296-3697-1-ND/377695)
U11,U14,U15 | SN74HCT125 | SO14-Wide | SN74HCT125DR | 3 | $0.12 | $0.34 | 6872 |  | $0.45 | $1.35 | 296-1206-1-ND (https://www.digikey.com/product-detail/en/texas-instruments/SN74HCT125DR/296-1206-1-ND/404916) | 5000 |  | $0.13 | $0.38 | 2437024 (http://it.farnell.com/texas-instruments/sn74hct125dr/gate-buffer-bus-3-stati-quad/dp/2437024?st=SN74HCT125DR) |  |  |  |  |  | NonStk |  | $0.12 | $0.34 | 76C3340 (http://www.newark.com/texas-instruments/sn74hct125dr/non-inverting-buffer-soic-14-full/dp/76C3340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) | 360 |  | $0.36 | $1.08 | 662-8266 (http://it.rs-online.com/web/c/?searchTerm=SN74HCT125DR)
U12 | 74LVC06AS14 | SOIC-14N | 74LVC06AS14-13 | 1 | $0.10 | $0.10 | NonStk |  | $0.10 | $0.10 | 74LVC06AS14-13DITR-ND (https://www.digikey.com/product-detail/en/diodes-incorporated/74LVC06AS14-13/74LVC06AS14-13DITR-ND/4249430)
U13 | SN74LS279 | SOIC16_Wide | SN74LS279ANSR | 1 | $0.00 | $0.00
U6 | LM7805 | LM7805 | MC7805BDTG | 1 | $0.39 | $0.39 | 20106 |  | $0.58 | $0.58 | MC7805BDTGOS-ND (https://www.digikey.com/products/en?keywords=MC7805BDTG) | NonStk |  | $0.61 | $0.61 | 1652336 (http://it.farnell.com/Search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) |  |  |  |  |  | NonStk |  | $0.58 | $0.58 | 71J5736 (http://www.newark.com/webapp/wcs/stores/servlet/Search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) | NonStk |  | $0.63 | $0.63 | 125-0048 (http://it.rs-online.com/web/p/regolatori-di-tensione-lineari/1250048/) | NonStk |  | $0.39 | $0.39 | MC7805BDTG (https://www.tme.eu/en/details/mc7805bdtg/unregulated-voltage-regulators/on-semiconductor/)
U3.DTA0,U3.DTD0,U3.DTC0,U3.DTB0 | MC74HC08AD | SOIC-14N | MC74HC08ADG | 4 | $0.13 | $0.51 | 17798 |  | $0.44 | $1.76 | MC74HC08ADGOS-ND (https://www.digikey.com/products/en?keywords=MC74HC08ADG) |  |  |  |  |  |  |  |  |  |  |  |  |  |  |  | 170 |  | $0.35 | $1.42 | 689-8705 (http://it.rs-online.com/web/p/porte-logiche/6898705/) | 520 |  | $0.13 | $0.51 | MC74HC08ADG (https://www.tme.eu/en/details/mc74hc08adg/gates-inverters/on-semiconductor/)
U4.DTC0,U4.DTD0,U4.DTB0,U4.DTA0 | MC74HC02ADG | SOIC-14N | MC74HC02ADG | 4 | $0.45 | $1.80 | 5831 |  | $0.45 | $1.80 | MC74HC02ADGOS-ND (https://www.digikey.com/products/en?keywords=MC74HC02ADG)
Distributors scraped by KiCost® v.0.1.46 |  |  |  |  |  |  |  | 0 |  |  |  |  | 0 |  |  |  |  | 0 |  |  |  |  | 0 |  |  |  |  | 0 |  |  |  |  | 0

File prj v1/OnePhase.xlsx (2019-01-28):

Prj: | OnePhase.xml |  |  |  | Board Qty: | 4
Co.: |  |  |  |  | Unit Cost: | $134.03
Prj date: | 2018-01-10 18:13:36 (file) |  |  |  | Total Cost: | $536.12 |  |  |  | $442.25 | 55 of 61 parts found |  |  |  | $319.83 | 11 of 61 parts found |  |  |  | $0.00 | 0 |  |  |  | $89.60 | 10 of 61 parts found |  |  |  | $7057.47 | 22 of 61 parts found |  |  |  | $374.09 | 16 of 61 parts found
$ date: | 2018-06-29 11:29:16
Global Part Info |  |  |  |  |  |  | Digi-Key |  |  |  |  | Farnell |  |  |  |  | Mouser |  |  |  |  | Newark |  |  |  |  | Rs Components |  |  |  |  | Tme
Refs | Value | Footprint | Manf# | Qty | Unit$ | Ext$ | Avail | Purch | Unit$ | Ext$ | Cat# | Avail | Purch | Unit$ | Ext$ | Cat# | Avail | Purch | Unit$ | Ext$ | Cat# | Avail | Purch | Unit$ | Ext$ | Cat# | Avail | Purch | Unit$ | Ext$ | Cat# | Avail | Purch | Unit$ | Ext$ | Cat#
C80,C81 | not used | Capacitor_Pol_15x6mm |  | 8 | $0.00 | $0.00
C13.1,C13.2,C16.1,C16.2 | 100nF | 0805_W | C0805C104K8RACTU | 16 | $0.14 | $2.18 | NonStk |  | $0.14 | $2.18 | 399-7999-1-ND (https://www.digikey.com/product-detail/en/kemet/C0805C104K8RACTU/399-7999-1-ND/3471722)
C14.1,C14.2 | 100pF | 0805_W | 08053C101KAT2A | 8 | $0.05 | $0.42 | NonStk |  | $0.05 | $0.42 | 08053C101KAT2A-ND (https://www.digikey.com/products/en?keywords=08053C101KAT2A)
C15.1,C15.2,C19.1,C19.2,C12.1,C12.2 | 2.2uF | 0805_W | 08053C225KAT2A | 24 | $0.24 | $5.81 | NonStk |  | $0.24 | $5.81 | 478-5719-1-ND (https://www.digikey.com/product-detail/en/avx-corporation/08053C225KAT2A/478-5719-1-ND/2136327) |  |  |  |  |  |  |  |  |  |  |  |  |  |  |  | NonStk |  | $284.37 | $6824.79 | 135-1403 (http://it.rs-online.com/web/p/condensatori-ceramici-multistrato/1351403/) | NonStk |  | $0.28 | $6.64 | 08053C225KAT2A (https://www.tme.eu/en/details/08053c225kat2a/0805-mlcc-smd-capacitors/avx/)
C18.1,C18.2,C24.1,C24.2,C21.1,C21.2,C8.1,C8.2,C9.1,C9.2,C17.1,C17.2,C22.1,C22.2,C10.1,C10.2,C20.1,C20.2,C11.1,C11.2,Cin2.1,Cin2.2,C23.1,C23.2 | 100nF | 0805_W | 08053C104KAT2A | 96 | $0.14 | $13.82 | NonStk |  | $0.14 | $13.82 | 478-3755-1-ND (https://www.digikey.com/product-detail/en/avx-corporation/08053C104KAT2A/478-3755-1-ND/1116453) |  |  |  |  |  |  |  |  |  |  |  |  |  |  |  | 1950 |  | $0.21 | $20.34 | 390-990 (http://it.rs-online.com/web/c/?searchTerm=08053C104KAT2A)
C25.1,C25.2 | 1nF | 0805_W | 08053C102KAT2A | 8 | $0.01 | $0.05 | NonStk |  | $0.05 | $0.42 | 08053C102KAT2A-ND (https://www.digikey.com/products/en?keywords=08053C102KAT2A) |  |  |  |  |  |  |  |  |  |  |  |  |  |  |  |  |  |  |  |  | NonStk |  | $0.01 | $0.05 | 08053C102KAT2A (https://www.tme.eu/en/details/08053c102kat2a/0805-mlcc-smd-capacitors/avx/)
C26-C29 | 220uF | Capacitor Eletrolitico - duplicate | B43305B9227M000 | 16 | $3.63 | $58.08 | 420 |  | $4.94 | $79.04 | 495-75814-ND (https://www.digikey.com/products/en?keywords=B43305B9227M000) | NonStk |  | $5.45 | $87.15 | 2283930 (http://it.farnell.com/Search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) |  |  |  |  |  | 968 |  | $3.63 | $58.08 | 52R2388 (http://www.newark.com/cornell-dubilier/slpx221m400e3p3/aluminum-electrolytic-capacitor/dp/52R2388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) | NonStk |  |  |  | 838-4924 (http://it.rs-online.com/web/p/condensatori-elettrolitici/8384924P/)
C30.1,C30.2,C31.1,C31.2 | 10nF | 0805_W | 08053C103KAT2A | 16 | $0.03 | $0.51 | NonStk |  | $0.05 | $0.84 | 08053C103KAT2A-ND (https://www.digikey.com/products/en?keywords=08053C103KAT2A) |  |  |  |  |  |  |  |  |  |  |  |  |  |  |  |  |  |  |  |  | NonStk |  | $0.03 | $0.51 | 08053C103KAT2A (https://www.tme.eu/en/details/08053c103kat2a/0805-mlcc-smd-capacitors/avx/)
C5.1,C5.2 | 47pF | 0805_W | C0805C473K8RAC7800 | 8 | $0.42 | $3.36 | 6863 |  | $0.42 | $3.36 | 399-15506-1-ND (https://www.digikey.com/product-detail/en/kemet/C0805C473K8RAC7800/399-15506-1-ND/7386904)
C7.1,C7.2 | 22nF | 0805_W | C0805C223K8RACTU | 8 | $0.06 | $0.52 | NonStk |  | $0.06 | $0.52 | C0805C223K8RACTU-ND (https://www.digikey.com/products/en?keywords=C0805C223K8RACTU)
Ca1 | 2.2uF | Capacitor_Pol_2Sizes | R463R422000M1M | 4 | $1.72 | $6.88 | 1608 |  | $1.72 | $6.88 | 399-5883-ND (https://www.digikey.com/products/en?keywords=R463R422000M1M)
Cin1.1,Cin1.2 | 1uF | 0805_W | 08053C105KAT2A | 8 | $0.22 | $1.74 | NonStk |  | $0.28 | $2.24 | 478-5030-1-ND (https://www.digikey.com/product-detail/en/avx-corporation/08053C105KAT2A/478-5030-1-ND/1888241) |  |  |  |  |  |  |  |  |  |  |  |  |  |  |  | NonStk |  | $0.33 | $2.63 | 136-4717 (http://it.rs-online.com/web/p/condensatori-ceramici-multistrato/1364717/) | 500 |  | $0.22 | $1.74 | 08053C105KAT2A (https://www.tme.eu/en/details/08053c105kat2a/0805-mlcc-smd-capacitors/avx/)
D3.1,D3.2,D8.1,D8.2,D12.1,D12.2,D7.1,D7.2,D2.1,D2.2,D5.1,D5.2,D10.1,D10.2,D4.1,D4.2,D13.1,D13.2,D9.1,D9.2,D1.1,D1.2 | BAT46Z | SOD-123 | BAT46ZFILM | 88 | $0.06 | $5.49 | 42988 |  | $0.27 | $23.41 | 497-5559-1-ND (https://www.digikey.com/product-detail/en/stmicroelectronics/BAT46ZFILM/497-5559-1-ND/1207051) | 6982 |  | $0.30 | $26.65 | 2341640 (http://it.farnell.com/stmicroelectronics/bat46zfilm/diodo-schottky-0-15a-100v-sod/dp/2341640?st=BAT46ZFILM) |  |  |  |  |  | 554 |  | $0.14 | $12.14 | 05X9522 (http://www.newark.com/stmicroelectronics/bat46zfilm/small-signal-diode-100-v-150-ma/dp/05X9522?st=BAT46ZFILM) | 1600 |  | $0.11 | $9.87 | 714-6850 (http://it.rs-online.com/web/p/diodi-rettificatori-e-schottky/7146850/) | 6366 |  | $0.06 | $5.49 | BAT46ZFILM (https://www.tme.eu/en/details/bat46zfilm/smd-schottky-diodes/st-microelectronics/)
D6.1,D6.2 | BZT52C8V2 | SOD-123 | BZT52C8V2-FDICT-ND | 8 | $0.23 | $1.84 | 2746 |  | $0.23 | $1.84 | BZT52C8V2-FDICT-ND (https://www.digikey.com/products/en?keywords=BZT52C8V2-FDICT-ND)
GateDriver.1#1,GateDriver.2#1 | MCP14A0601 - p1/2 | SOIC-8N | MIC4420YM-TR | 8 | $1.20 | $9.60 | 7403 |  | $1.58 | $12.64 | 576-1189-1-ND (https://www.digikey.com/product-detail/en/microchip-technology/MIC4420YM-TR/576-1189-1-ND/771866) | NonStk |  | $1.97 | $15.75 | 2100309 (http://it.farnell.com/micrel-semiconductor/mic4420ym-tr/driver-mosfet-non-inv-ls-6a-8soic/dp/2100309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) |  |  |  |  |  | NonStk |  | $1.20 | $9.60 | 11AC9669 (http://www.newark.com/webapp/wcs/stores/servlet/Search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) | 1650 |  | $1.67 | $13.35 | 910-2029 (http://it.rs-online.com/web/p/driver-mosfet/9102029/)
GateDriver.1#2,GateDriver.2#2 | MCP14A0601 - p2/2 | SOIC-8N | MIC4422ZM | 8 | $1.55 | $12.40 | 256 |  | $1.99 | $15.92 | 576-1793-5-ND (https://www.digikey.com/product-detail/en/microchip-technology/MIC4422ZM/576-1793-5-ND/1029860) |  |  |  |  |  |  |  |  |  |  |  |  |  |  |  |  |  |  |  |  | 299 |  | $1.55 | $12.40 | MIC4422ZM (https://www.tme.eu/en/details/mic4422zm/mosfetigbt-drivers/microchip-micrel/)
P1 | Bornier | 3 Pin Borner | 1935174 | 4 | $0.70 | $2.81 |  |  |  |  |  |  |  |  |  |  |  |  |  |  |  |  |  |  |  |  | 70 |  | $0.70 | $2.81 | 548-7244 (http://it.rs-online.com/web/c/?searchTerm=1935174)
P2,P3 | Header 3 | HDR1X3 |  | 8 | $0.00 | $0.00
Pin_A1,DCn0,DCp0 | screw | Power conector | 7799 | 12 | $15.02 | $180.23 |  |  |  |  |  | 18 |  | $15.02 | $180.23 | 1778765 (http://it.farnell.com/Search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) |  |  |  |  |  |  |  |  |  |  |  |  |  |  |  | NonStk |  | $18.09 | $217.08 | 407799 (https://www.tme.eu/en/details/407799/circuit-breakers/legrand/s-302-c13-dx/)
Q5#1,Q6#1,Q7#1,Q8#1 | IRFP260 - p1/5 | TO227 | 4180G | 16 | $1.25 | $20.02 |  |  |  |  |  |  |  |  |  |  |  |  |  |  |  |  |  |  |  |  | 35 |  | $1.25 | $20.02 | 171-512 (http://it.rs-online.com/web/p/file-di-contatti-da-pcb/0171512/)
Q5#2,Q6#2,Q7#2,Q8#2 | IRFP260 - p2/5 | TO227 | RM3X10MM 2701 | 16 | $0.45 | $7.20 | 11992 |  | $0.45 | $7.20 | 335-1148-ND (https://www.digikey.com/products/en?keywords=RM3X10MM+2701)
Q5#3,Q6#3,Q7#3,Q8#3 | IRFP260 - p3/5 | TO227 | IRFP260MPBF | 16 | $1.44 | $23.04 | 659 |  | $2.98 | $47.66 | IRFP260MPBF-ND (https://www.digikey.com/products/en?keywords=IRFP260MPBF) |  |  |  |  |  |  |  |  |  |  |  |  |  |  |  | 300 |  | $2.47 | $39.57 | 124-8763 (http://it.rs-online.com/web/p/transistor-mosfet/1248763/) | 712 |  | $1.44 | $23.04 | IRFP260MPBF (https://www.tme.eu/en/details/irfp260mpbf/tht-n-channel-transistors/infineon-irf/)
Q5#4,Q6#4,Q7#4,Q8#4 | IRFP260 - p4/5 | TO227 | 28N65M2 | 16 | $2.32 | $37.13 | 1771 |  | $3.01 | $48.11 | 497-15575-5-ND (https://www.digikey.com/product-detail/en/stmicroelectronics/STW28N65M2/497-15575-5-ND/5244948) |  |  |  |  |  |  |  |  |  |  |  |  |  |  |  | NonStk |  | $2.32 | $37.13 | 168-8840 (http://it.rs-online.com/web/p/transistor-mosfet/1688840/)
Q5#5,Q6#5,Q7#5,Q8#5 | IRFP260 - p5/5 | TO227 | C3M0280090D | 16 | $3.64 | $58.24 | 890 |  | $3.64 | $58.24 | C3M0280090D-ND (https://www.digikey.com/products/en?keywords=C3M0280090D) |  |  |  |  |  |  |  |  |  |  |  |  |  |  |  | NonStk |  | $3.76 | $60.13 | 915-8842 (http://it.rs-online.com/web/p/transistor-mosfet/9158842/) | NonStk |  | $5.10 | $81.60 | C3M0280090D (https://www.tme.eu/en/details/c3m0280090d/tht-n-channel-transistors/wolfspeedcree/)
Q1.1,Q1.2 | BC857 | SOT-23-TT3_N | BC857BLT1G | 8 | $0.01 | $0.09 | 1973 |  | $0.12 | $0.96 | BC857BLT1GOSCT-ND (https://www.digikey.com/product-detail/en/on-semiconductor/BC857BLT1G/BC857BLT1GOSCT-ND/917843) |  |  |  |  |  |  |  |  |  |  |  |  |  |  |  | 21000 |  | $0.02 | $0.16 | 545-2771 (http://it.rs-online.com/web/p/transistor-bipolari/5452771/) | 33000 |  | $0.01 | $0.09 | BC857BLT1G (https://www.tme.eu/en/details/bc857blt1g/pnp-smd-transistors/on-semiconductor/)
Q2.1,Q2.2 | BC847 | SOT-23-TT3_N | BC847BLT1G | 8 | $0.02 | $0.13 | 191254 |  | $0.12 | $0.96 | BC847BLT1GOSCT-ND (https://www.digikey.com/product-detail/en/on-semiconductor/BC847BLT1G/BC847BLT1GOSCT-ND/917834) | 6000 |  | $0.04 | $0.34 | 2317816 (http://it.farnell.com/on-semiconductor/bc847blt1g/transistor-npn-45v-100ma-sot-23/dp/2317816?st=BC847BLT1G) |  |  |  |  |  | 48834 |  | $0.12 | $0.97 | 88H4566 (http://www.newark.com/on-semiconductor/bc847blt1g/bipolar-transistor-npn-45v-sot/dp/88H4566?st=BC847BLT1G) | NonStk |  | $0.02 | $0.13 | 545-2759 (http://it.rs-online.com/web/c/?searchTerm=BC847BLT1G) | 23266 |  | $0.03 | $0.26 | BC847BLT1G (https://www.tme.eu/en/details/bc847blt1g/npn-smd-transistors/on-semiconductor/)
Q3.1,Q3.2 | BC857B | SOT-23-TT3_N | BC857BLT1G | 8 | $0.01 | $0.09 | 1973 |  | $0.12 | $0.96 | BC857BLT1GOSCT-ND (https://www.digikey.com/product-detail/en/on-semiconductor/BC857BLT1G/BC857BLT1GOSCT-ND/917843) |  |  |  |  |  |  |  |  |  |  |  |  |  |  |  | 21000 |  | $0.02 | $0.16 | 545-2771 (http://it.rs-online.com/web/p/transistor-bipolari/5452771/) | 33000 |  | $0.01 | $0.09 | BC857BLT1G (https://www.tme.eu/en/details/bc857blt1g/pnp-smd-transistors/on-semiconductor/)
Q4.1,Q4.2 | BC847B | SOT-23-TT3_N | BC847BLT1G | 8 | $0.02 | $0.13 | 191251 |  | $0.12 | $0.96 | BC847BLT1GOSCT-ND (https://www.digikey.com/product-detail/en/on-semiconductor/BC847BLT1G/BC847BLT1GOSCT-ND/917834) |  |  |  |  |  |  |  |  |  |  |  |  |  |  |  | NonStk |  | $0.02 | $0.13 | 545-2759 (http://it.rs-online.com/web/c/?searchTerm=BC847BLT1G) | 23266 |  | $0.03 | $0.26 | BC847BLT1G (https://www.tme.eu/en/details/bc847blt1g/npn-smd-transistors/on-semiconductor/)
R11.1,R11.2 | 2.0k | 0805_W | RMCF0805JT2K00 | 8 | $0.10 | $0.80 | 17 |  | $0.10 | $0.80 | RMCF0805JT2K00CT-ND (https://www.digikey.com/product-detail/en/stackpole-electronics-inc/RMCF0805JT2K00/RMCF0805JT2K00CT-ND/1942562)
R12.1,R12.2,R16.1,R16.2,R10.1,R10.2 | 22k | 0805_W | RMCF0805JT22K0 | 24 | $0.02 | $0.41 | 41619 |  | $0.02 | $0.41 | RMCF0805JT22K0CT-ND (https://www.digikey.com/product-detail/en/stackpole-electronics-inc/RMCF0805JT22K0/RMCF0805JT22K0CT-ND/1942581)
R14.1,R14.2 | 22k | 0805_W | RMCF0805JT560K | 8 | $0.10 | $0.80 | 2755 |  | $0.10 | $0.80 | RMCF0805JT560KCT-ND (https://www.digikey.com/product-detail/en/stackpole-electronics-inc/RMCF0805JT560K/RMCF0805JT560KCT-ND/7906832)
R15.1,R15.2,R36,R37,R17.1,R17.2,R1.1,R1.2 | 10k | 0805_W | RMCF0805JT10K0 | 32 | $0.02 | $0.54 | 479445 |  | $0.02 | $0.54 | RMCF0805JT10K0CT-ND (https://www.digikey.com/product-detail/en/stackpole-electronics-inc/RMCF0805JT10K0/RMCF0805JT10K0CT-ND/1942577)
R18.1,R18.2 | 47k | 0805_W | RMCF0805JT5K60 | 8 | $0.10 | $0.80 | 95771 |  | $0.10 | $0.80 | RMCF0805JT5K60CT-ND (https://www.digikey.com/product-detail/en/stackpole-electronics-inc/RMCF0805JT5K60/RMCF0805JT5K60CT-ND/1942572)
R19.1,R19.2,C3.1,C3.2,C2.1,C2.2,C6.1,C6.2,R30.1,R30.2,C4.1,C4.2,C1.1,C1.2 | not used | 0805_W |  | 56 | $0.00 | $0.00
R2.1,R2.2,R3.1,R3.2,R6.1,R6.2,R5.1,R5.2,R4.1,R4.2,R7.1,R7.2,R8.1,R8.2,R9.1,R9.2 | 100k | 0805_W | RMCF0805JT100K | 64 | $0.01 | $0.37 | 319357 |  | $0.02 | $1.09 | RMCF0805JT100KCT-ND (https://www.digikey.com/product-detail/en/stackpole-electronics-inc/RMCF0805JT100K/RMCF0805JT100KCT-ND/1942592) | NonStk |  | $0.01 | $0.37 | 1815021 (http://it.farnell.com/Search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) |  |  |  |  |  | NonStk |  | $0.01 | $0.70 | 49P0229 (http://www.newark.com/vishay-dale/crcw0805100kjntb/crcw0805-100k-5-200-rt5/dp/49P0229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)
R20.1,R20.2 | 15k | 0805_W | RMCF0805JT15K0 | 8 | $0.10 | $0.80 | 63908 |  | $0.10 | $0.80 | RMCF0805JT15K0CT-ND (https://www.digikey.com/product-detail/en/stackpole-electronics-inc/RMCF0805JT15K0/RMCF0805JT15K0CT-ND/1942578)
R21.1,R21.2 | 33k | 0805_W | RMCF0805JT33K0 | 8 | $0.002 | $0.02 | 151781 |  | $0.10 | $0.80 | RMCF0805JT33K0CT-ND (https://www.digikey.com/product-detail/en/stackpole-electronics-inc/RMCF0805JT33K0/RMCF0805JT33K0CT-ND/1942585) | 14843 |  | $0.03 | $0.27 | 1514855 (http://it.farnell.com/Search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) |  |  |  |  |  | NonStk |  | $0.002 | $0.02 | 32AC2763 (http://www.newark.com/webapp/wcs/stores/servlet/Search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)
R22.1,R22.2 | 330R | 0805_W | RMCF0805JT330R | 8 | $0.10 | $0.80 | 189867 |  | $0.10 | $0.80 | RMCF0805JT330RCT-ND (https://www.digikey.com/product-detail/en/stackpole-electronics-inc/RMCF0805JT330R/RMCF0805JT330RCT-ND/1942547)
R23.1,R23.2 | 3.3k | 0805_W | RMCF0805JT3k30 | 8 | $0.10 | $0.80 | 7696 |  | $0.10 | $0.80 | RMCF0805JT3K30CT-ND (https://www.digikey.com/product-detail/en/stackpole-electronics-inc/RMCF0805JT3K30/RMCF0805JT3K30CT-ND/1942567)
R24.1,R24.2,R25.1,R25.2 | 100R | 0805_W | RMCF0805JT100R | 16 | $0.003 | $0.05 | 431038 |  | $0.02 | $0.27 | RMCF0805JT100RCT-ND (https://www.digikey.com/product-detail/en/stackpole-electronics-inc/RMCF0805JT100R/RMCF0805JT100RCT-ND/1942539) | 32 |  | $0.20 | $3.25 | 1739215 (http://it.farnell.com/vishay/crcw0805100rjneaif/res-film-spesso-100r-5-0-125w/dp/1739215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) |  |  |  |  |  | NonStk |  | $0.003 | $0.05 | 32AC2740 (http://www.newark.com/webapp/wcs/stores/servlet/Search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)
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

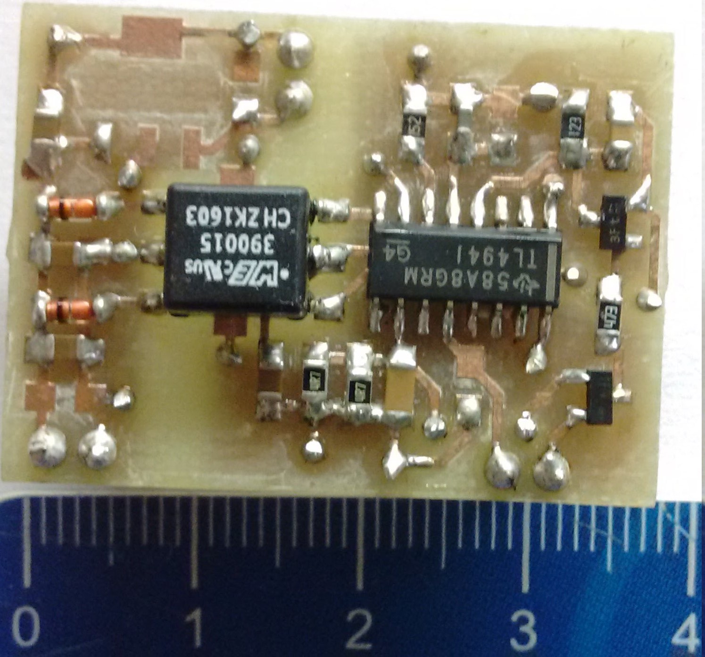
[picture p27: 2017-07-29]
prj v1/Assemblies/2016-10-05_IsolatedSupplier2(top).jpg

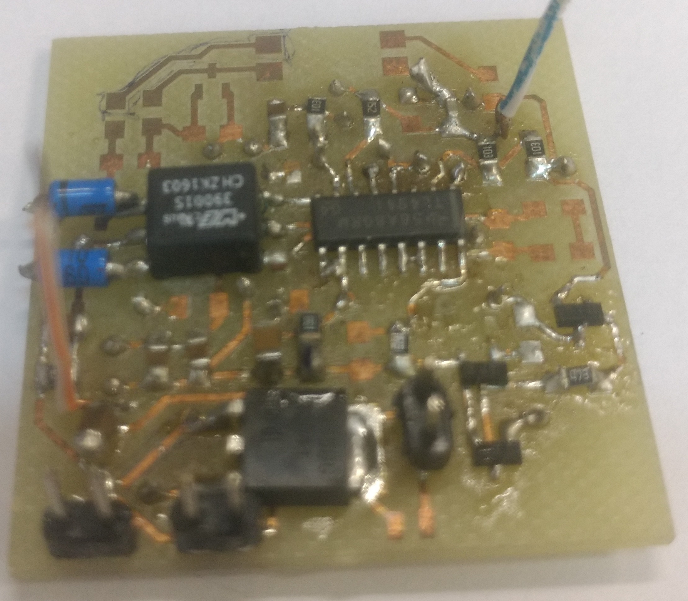
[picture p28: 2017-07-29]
prj v1/Assemblies/2016-10-01_IsolatedSupplier1.jpg

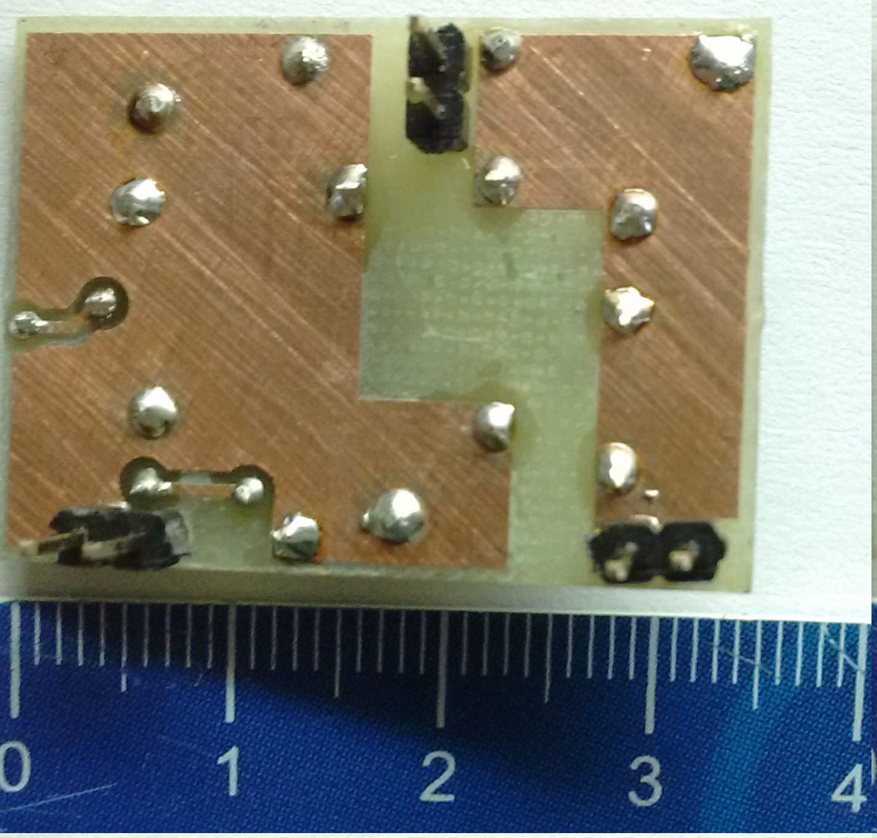
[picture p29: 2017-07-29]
prj v1/Assemblies/2016-10-05_IsolatedSupplier2(bottom).jpg

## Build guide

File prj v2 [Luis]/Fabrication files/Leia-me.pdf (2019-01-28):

Nessa pasta, estão presentes os arquivos para a fabricação de duas placas, nomeadas de MainBoard e GateDriver_board;

Arquivos fornecidos:

MainBoard:

1. Gerbers;

### 2. NC drill files

a. Arquivo MainBoard_PCB-RoundHoles.TXT mapeia os furos a serem feitos com broca normal
b. Arquivo MainBoard_PCB-SlotHoles.TXT mapeia os furos a serem feitos com fresa pois não são circulares;

### 3. Drill Drawing indicando os furos metalizados e não metalizados

4. Stack da placa;

GateDriver_board:

1. Gerbers;

### 2. NC drill files

a. Apenas um arquivo, pois todos os furos são circulares;
3. Não é incluído o DrillDrawing pois todos os furos devem ser metalizados;
4. Stack da placa;

Caracteristicas de cada placa:

MainBoard:

- Tanto bottom quanto top layer com 2oz;
- FR-4 1.6mm de espessura;

GateDriver_board:

- Tanto bottom quanto top layer com 1/2oz;
- FR-4 1.6mm de espessura;

Qualquer dúvida, favor entrar em contato através do email ou telefone abaixo:

Email: luis.possatti@gmail.com

Tel: 019 9 9972 5082

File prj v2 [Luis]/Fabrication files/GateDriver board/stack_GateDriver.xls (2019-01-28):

Board Stack Report
Stack Up |  | Layer Stack
Layer | Board Layer Stack | Name | Material | Thickness | Constant
1 |  | Top Paste
2 |  | Top Overlay
3 |  | Top Solder | Solder Resist | 0,010mm | 3,5
4 |  | Top Layer | Copper | 0,018mm
5 |  | Dielectric 1 | FR-4 | 1,600mm | 4,8
6 |  | Bottom Layer | Copper | 0,018mm
7 |  | Bottom Solder | Solder Resist | 0,010mm | 3,5
8 |  | Bottom Overlay
9 |  | Bottom Paste
 | Height : 1,691mm

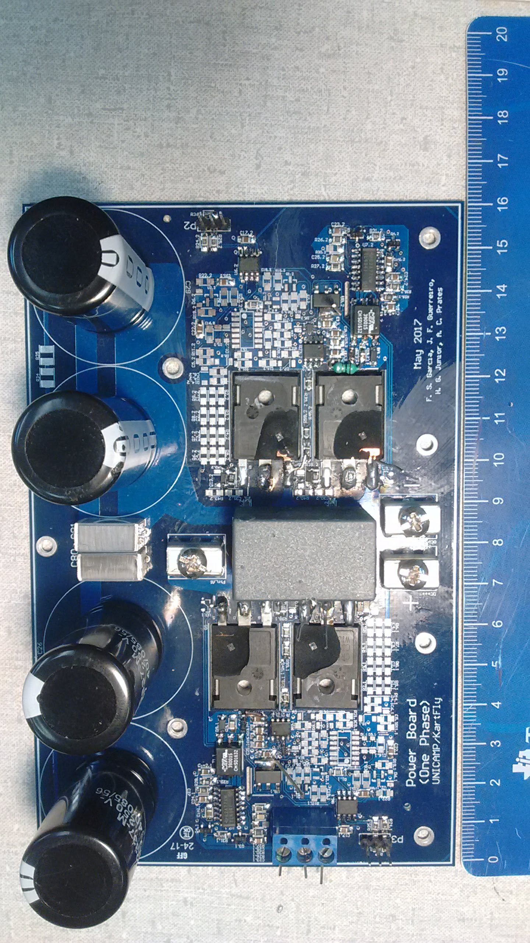
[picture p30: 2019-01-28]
prj v1/Assemblies/2017-06-01 One phase [FSG] (with errors)/SiC 200V 200kHz 3A (1).jpg

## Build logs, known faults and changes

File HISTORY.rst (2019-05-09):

History of the first develop step of each part of the inverter until get a complete inverter.

2018-04-??
------------

1. Migrated to Altium 18.
2. Added 3D model to the components and organized the library of the project;
3. Changed the gate drive to Schmitt trigger model with enable pin (removed the little AND port);
4. Changed the isolated power supply circuit to a RECOM module and add a EMC (Conducted and Radiated Filter) filter;
5. Improved the gate drive circuit to avoid cross-talk trigger;
5. Gate drive and protection goes to a vertical modular board;
6. Changed the base power design to a H-bridge (2 phases) instead a arm (1 phase).

Layout by Luis H. D. Possatti.
Revision by Hildo and Joel.

2017-06-13
------------

- **Folder:** 2017-06-13 Logics only prototype [HGJr]
- **Images:** "2017-06-29 Logic (bottom).jpg" & "2017-06-29 Logic (top).jpg"

## Improvements did

1. Improved the main power supply layout to reduce the size and improve EMI.

2017-06-01
------------

- **Folder:** 2017-06-01 One phase  [FSG] (with errors)
- **Images:** "2017-06-27 One phase 3.jpg" & "2017-08-06 One phase 3.jpg"

Optimized layout of one arm including the snubber gate circuit. Optimized the current protection logic by Hildo, Joel and Fellipe.

Layout by Fellipe.

## Improvements did

1. Changed the optical isolator Si8421Ad to Si8422 (21 model goes HIGH when burn and 22 goes LOW);
2. Reduced the size;
3. Top silk and footprints in standards to factory production;
4. Calibrated the gate snubber circuit component values (not in this schematic, updated to next version).
5. Changed the gate drive MIC4420 + AND gate 74HCT1G08 to the ???? gate drive with Schmitt trigger input and enable terminal (not in this schematic, updated to next version).

## Diagnosed errors / warnings

1. Replaced the input pair 8-9 and 10-11. Corrected in tests by wires;
2. High interference.
Tested up to 100V, 100KHz.

2017-05-17
------------

- **Images:** "Supplier (bottom).jpg" & "Supplier (top).jpg"

Tested the main power supply to provide energy to all the board in final project. Use the automotive IC LM25011.

Layout recomended by the manufacturer.

2017-03-13
------------

- **Folder:** "2017-03-13 One phase prototype [HGJr]"
- **Images:** "2017-04-28 One phase 2 (bottom).jpg" & "2017-04-28 One phase 2 (top).jpg"

One arm inverter prototype, isolated source + protections + gate drive.
Layout by Hildo.

Testes up to 200V of DC link with 150kHz and 5A. With lest voltage, tested with high frequency, 300kHz.

It was necessary add some extra gate ("snubber") circuit to avoid the voltage overshoot in the transistor turn-on.

## Improvements did

1. Tested the Si8421 IC isolator (LOW default output) at the place of Si8422 (HIGH default output). Diagnosed a problem when this IC burn, may drive on the transistors. This correction was not included in the layout;
2. Better isolated supply layout (the data pins are exchanged).

2017-04-03
------------

- **Images:** "One phase (bottom).jpg" & "One phase (top).jpg"

First version of one arm of the inverter. Protections does not worked.

Layout by Arthur.

2016-10-05
------------

- **Images:** "2016-10-05 Isolated supplier 2 (bottom).jpg" & "2016-10-05 Isolated supplier 2 (top).jpg"

Improved layout by Fellipe, Arthur and Hildo.

2016-10-01
------------

- **Image:** "2016-10-01 Isolated supplier 1.jpg"

Isolated power supplier to the gate drivers tested and working at 400kHz. It will be used as gate driver power source.

Schematic by Fellipe and layout by Arthur.

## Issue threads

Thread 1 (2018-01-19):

Remove not used parts

hildogjr, 2018-01-19:
Remove the not used parts of the schematic and the layout:
- Check the isolated power supply
- Capacitor of speed-up of the voltage divider in the protections

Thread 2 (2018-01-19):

Do a automatic price BoM

hildogjr, 2018-01-19:
Do a automatic Bill of Materials with prices in the main distributors. Use the FREE tool KiCost
https://github.com/xesscorp/KiCost/issues

hildogjr, 2018-01-19:
On last releases of KiCost was revised the capability of read XML Altium BoM and group the components. Now the tool is able to this work.

Closed 2018-01-19.

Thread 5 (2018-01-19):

Footprint optimization

hildogjr, 2018-01-19:
Change all 0805 footprint from WIDE to normal to reduce the space used in the board.
Standardize the IC footprints (some of them are rounded pads and others squared ones).
Improve the TO247 horizontal cut board assembly (improve the hole of the central pin, this as causing some mechanical damage in the replacement).

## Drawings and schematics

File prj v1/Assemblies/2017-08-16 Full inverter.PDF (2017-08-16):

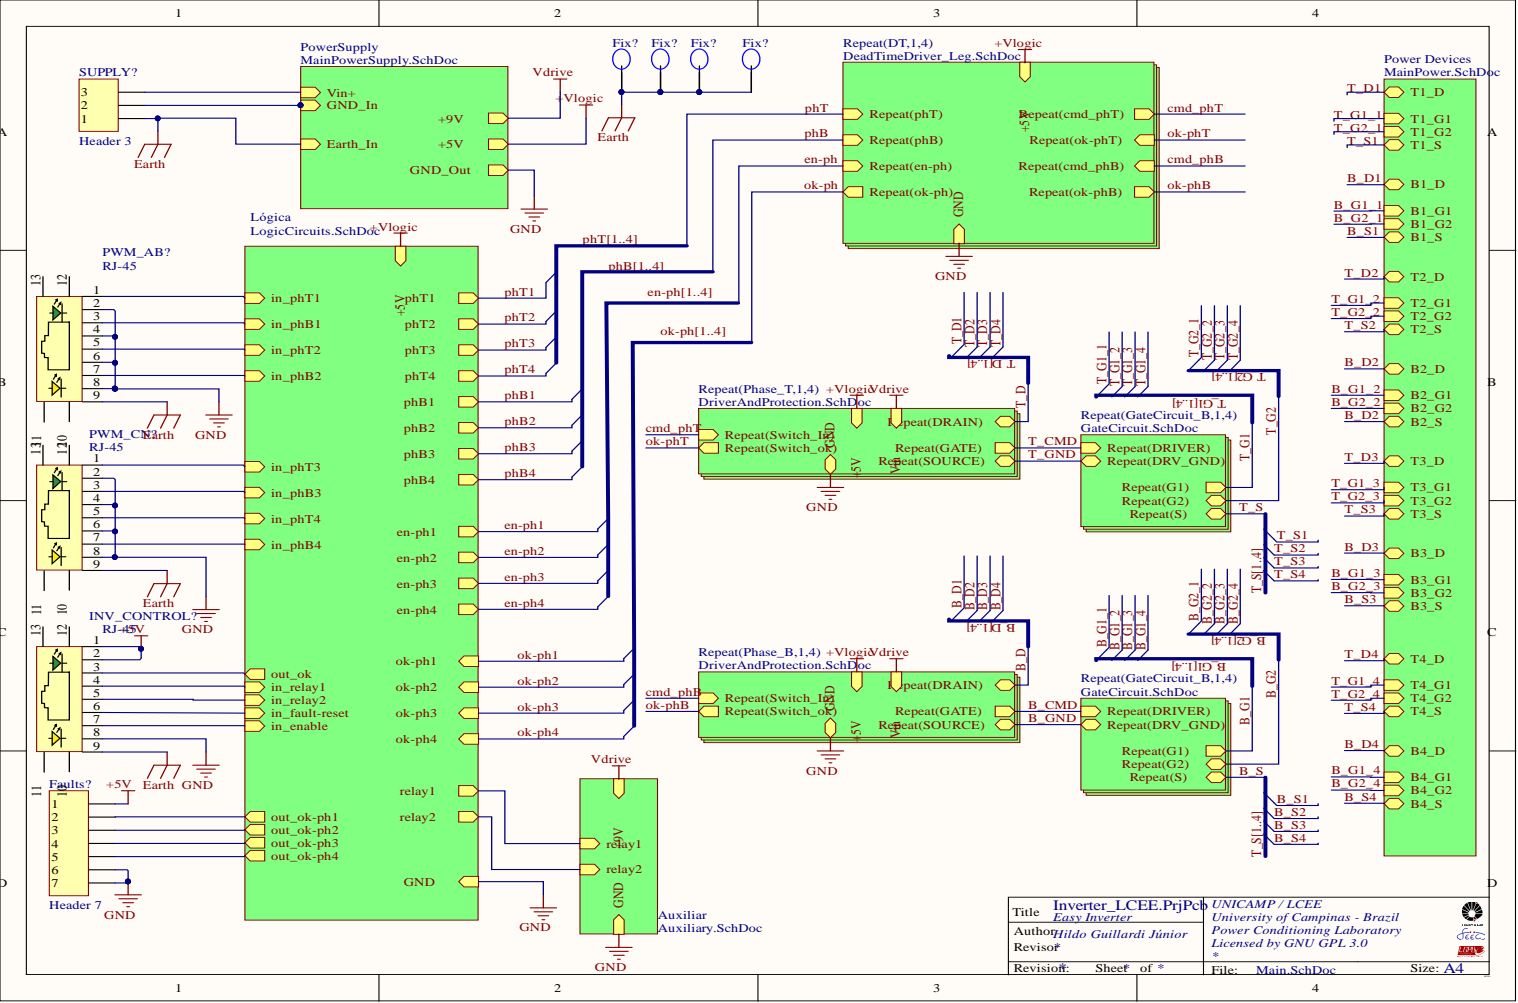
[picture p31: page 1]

en-p h | cmd _ p h B

Dri | verA | n

Repeat(DRAIN ) i tch _In ) i tch _ o k ) Repeat(G AT E ) Repeat(SO URCE )

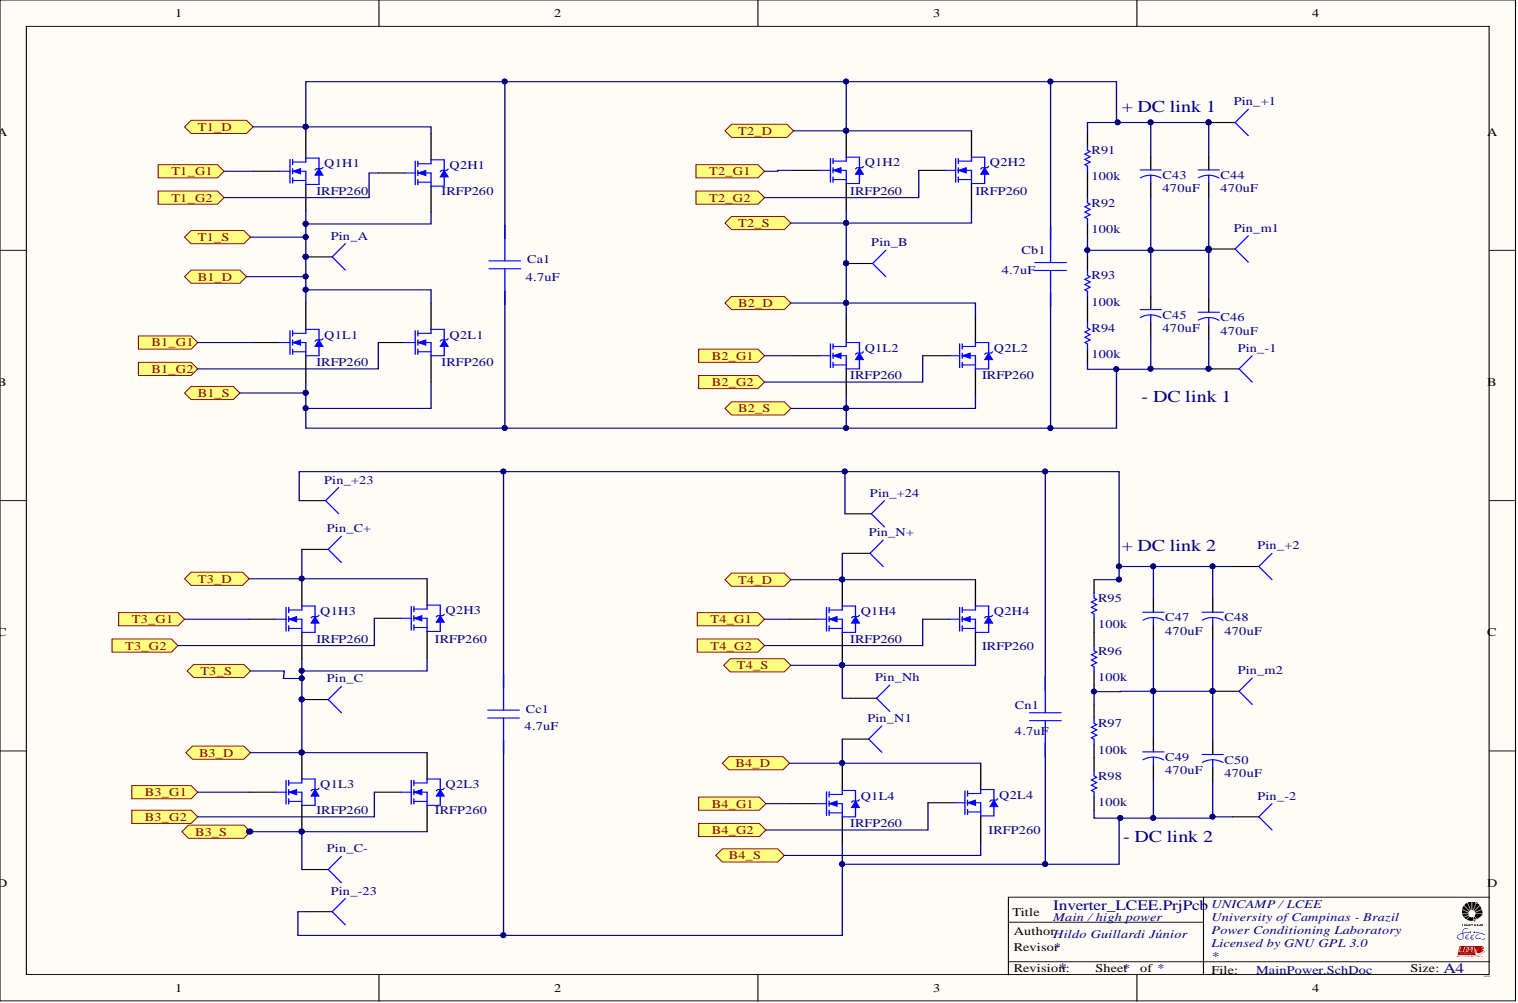
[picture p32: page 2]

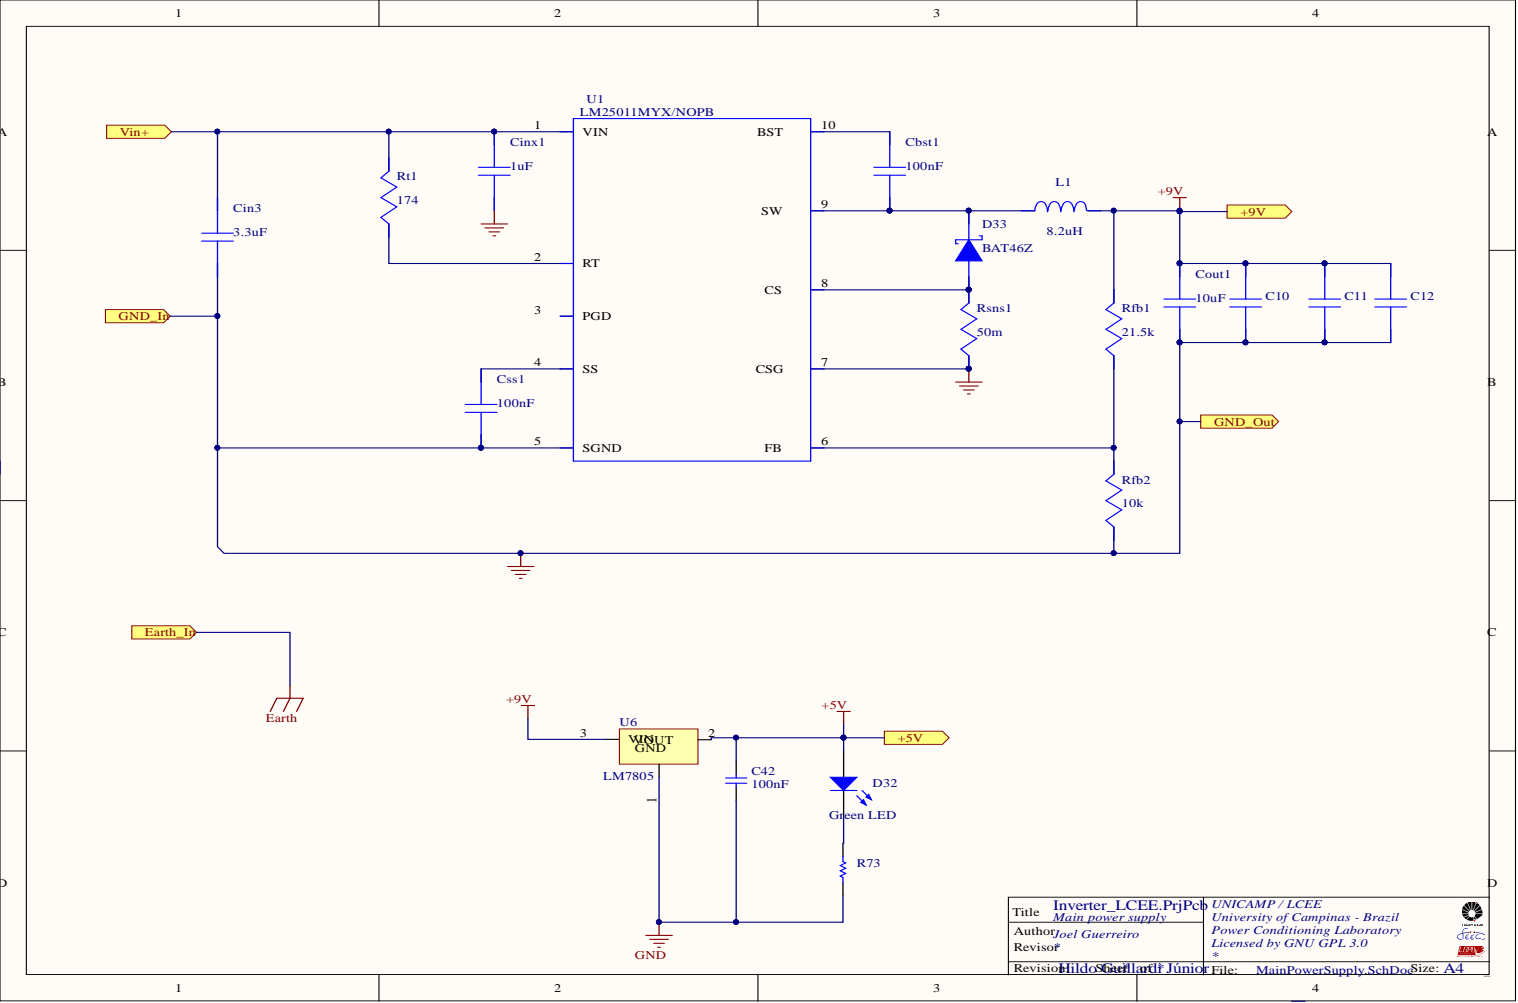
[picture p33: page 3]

Main power supply Inverter_LCEE.PrjPcb

UNICAMP / LCEE
University of Campinas - Brazil
Power Conditioning Laboratory
Licensed by GNU GPL 3.0

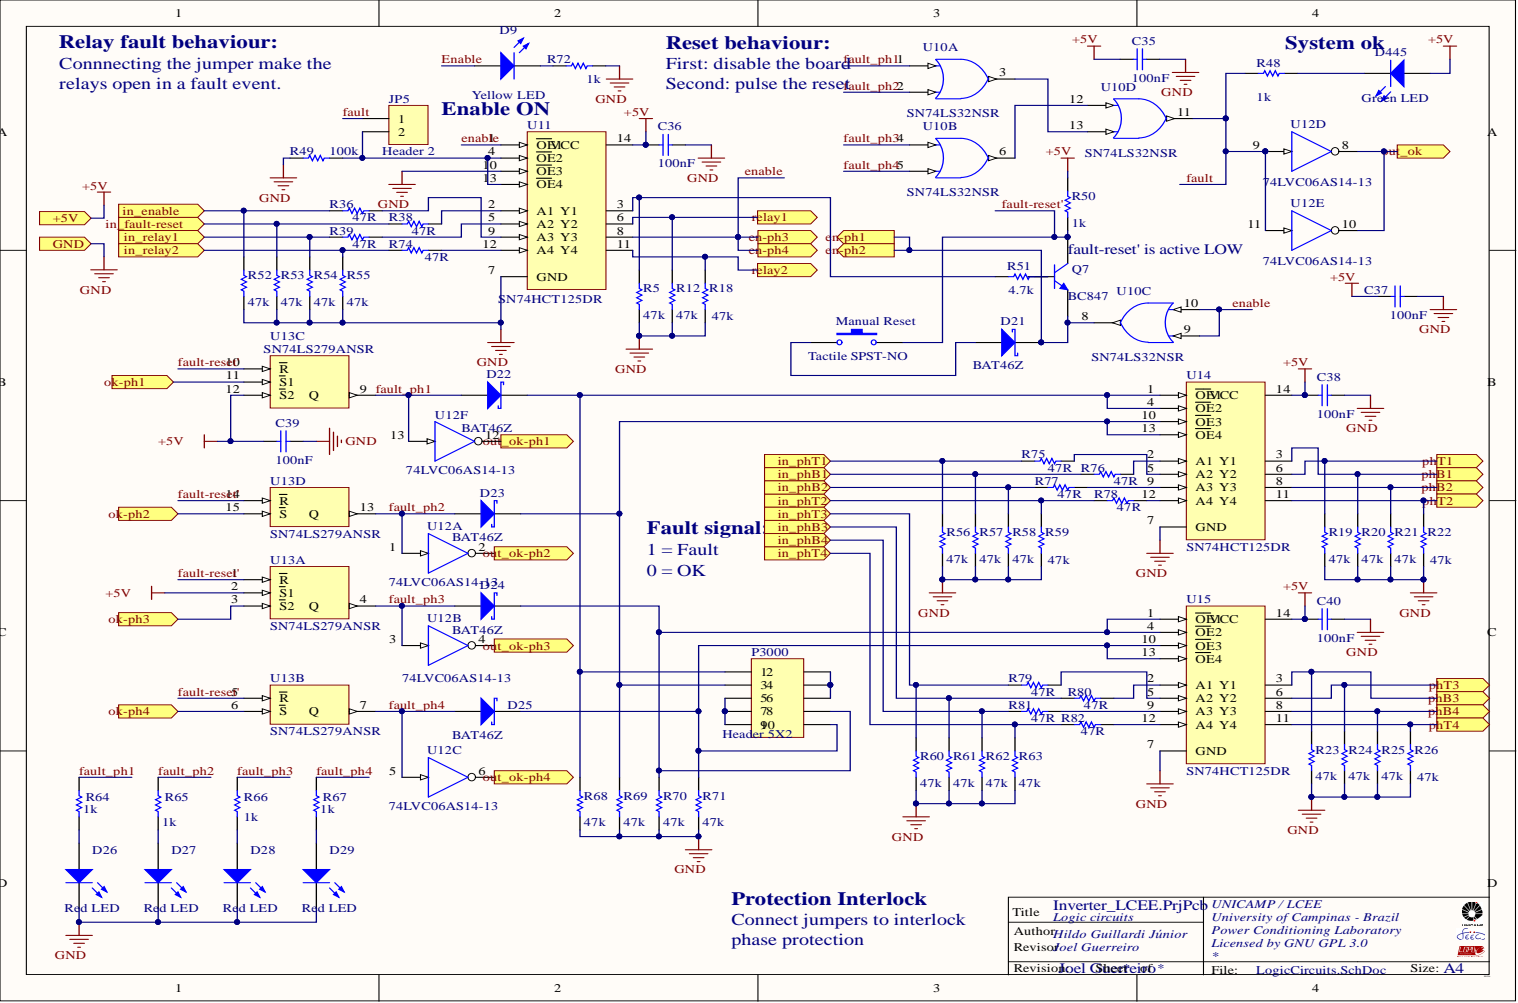
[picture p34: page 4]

Relay fault behaviour:
Connnecting the jumper make the
relays open in a fault event.

Reset behaviour:
First: disable the board
Second: pulse the reset

OE3 10
OE4 13

fault

fault-reset' is active LOW

Protection Interlock
Connect jumpers to interlock
phase protection

UNICAMP / LCEE
University of Campinas - Brazil

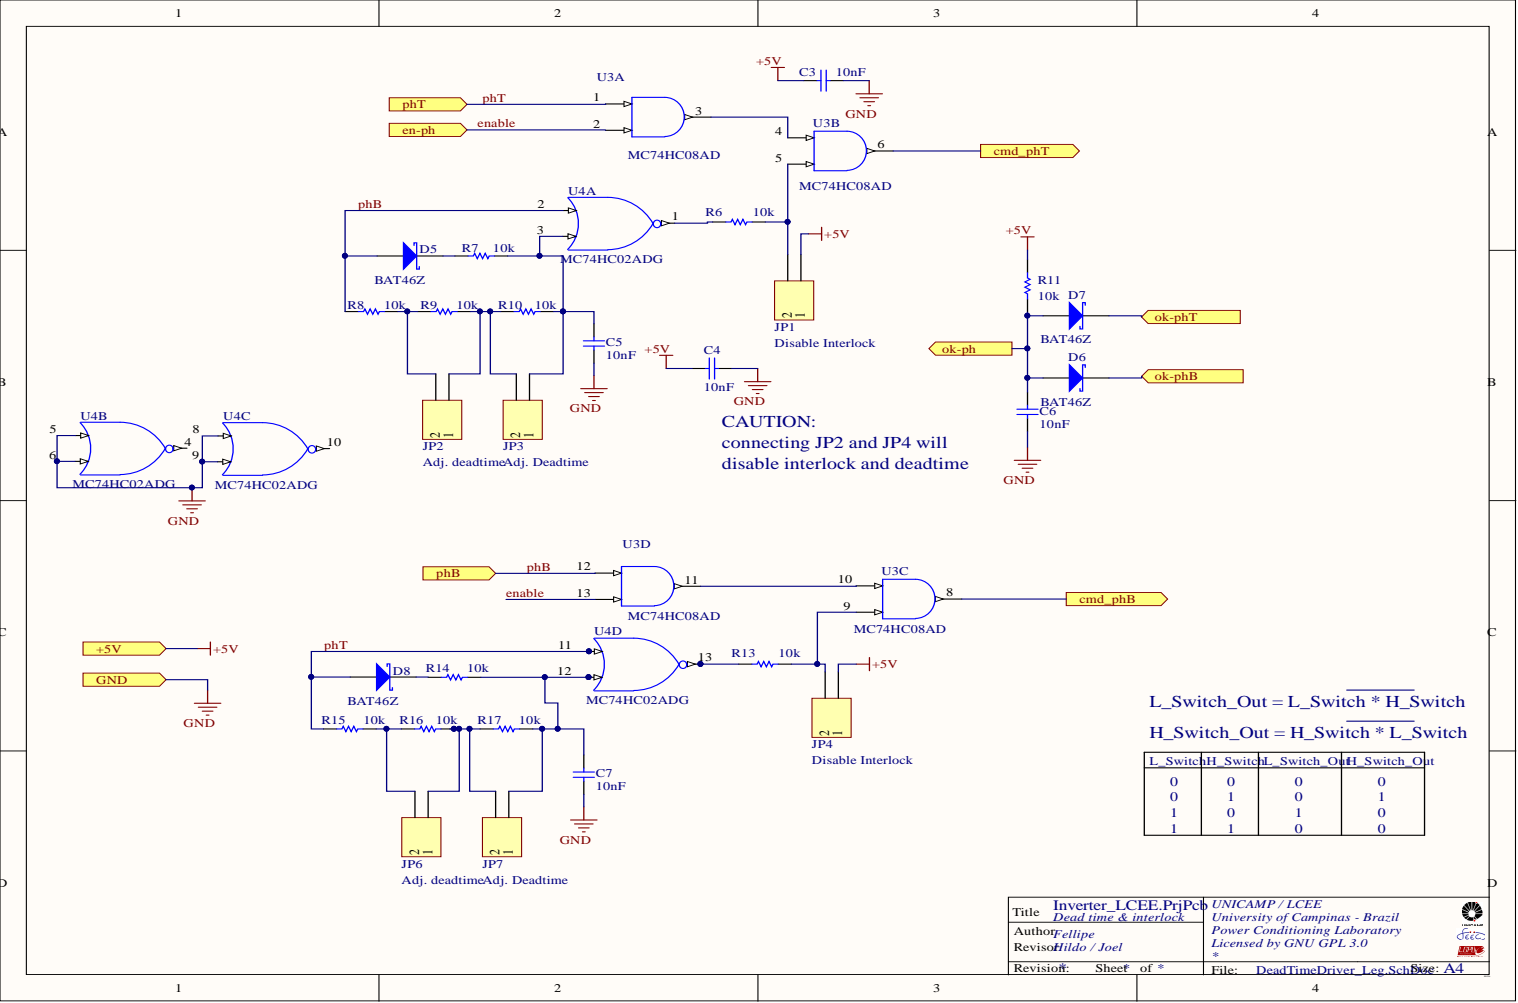
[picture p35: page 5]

Dead time & interlock Inverter_LCEE.PrjPcb

UNICAMP / LCEE
University of Campinas - Brazil

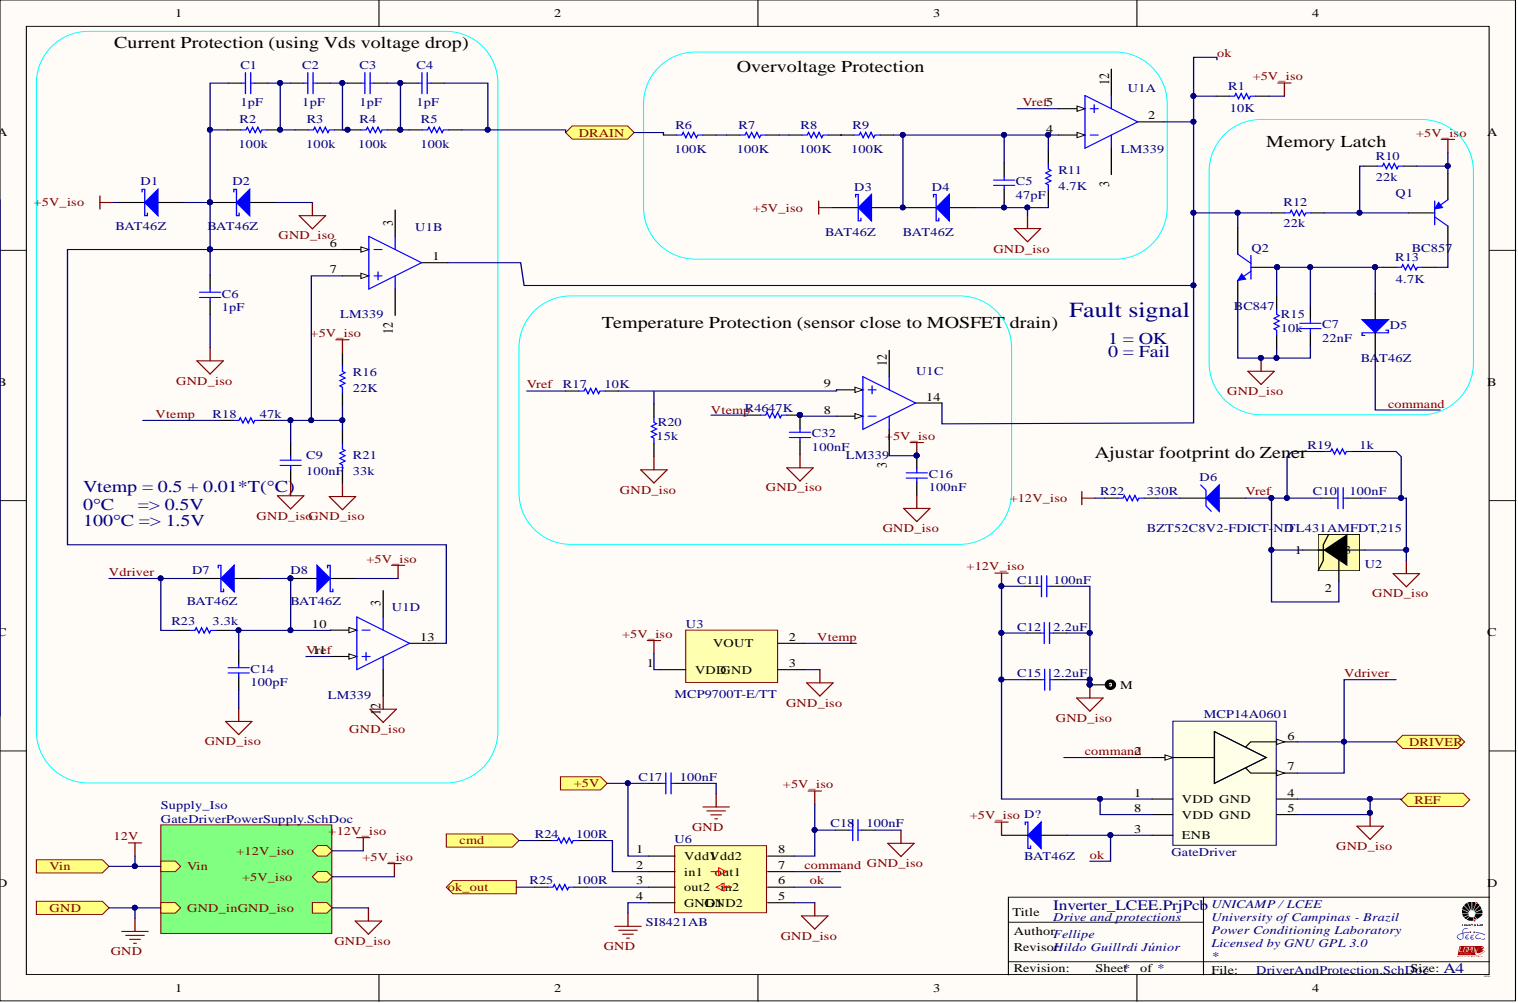
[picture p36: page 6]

Current Protection (using Vds voltage drop)

Temperature Protection (sensor close to MOSFET drain)

Ajustar footprint do Zener

Drive and protections Inverter_LCEE.PrjPcb

UNICAMP / LCEE
University of Campinas - Brazil

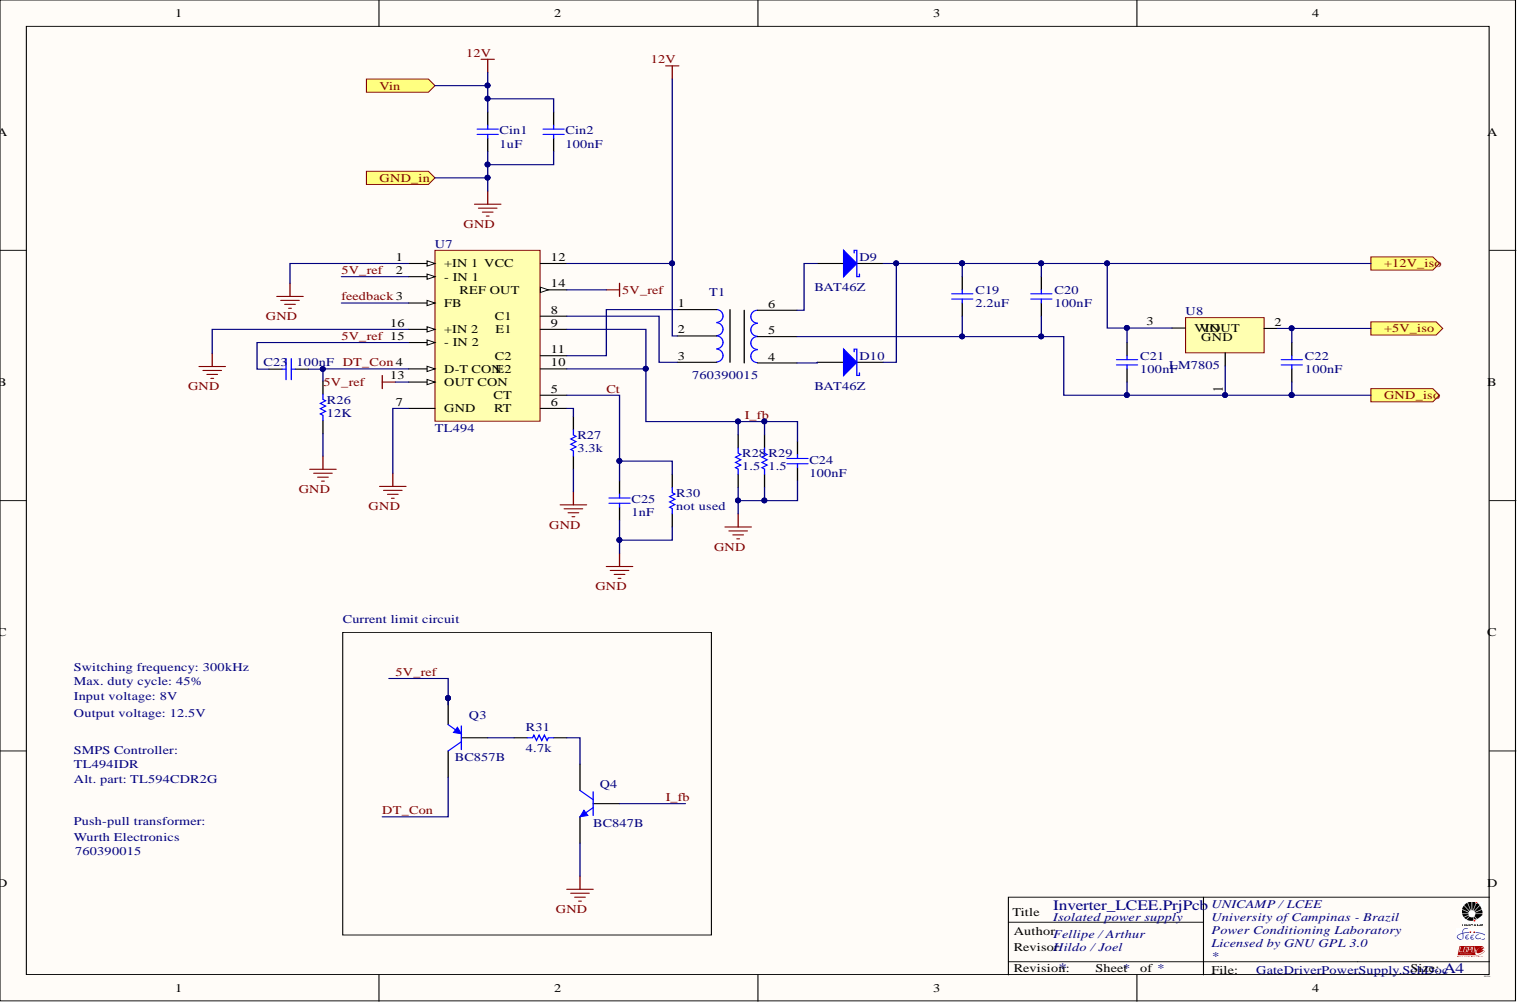
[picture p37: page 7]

Isolated power supply Inverter_LCEE.PrjPcb

UNICAMP / LCEE
University of Campinas - Brazil

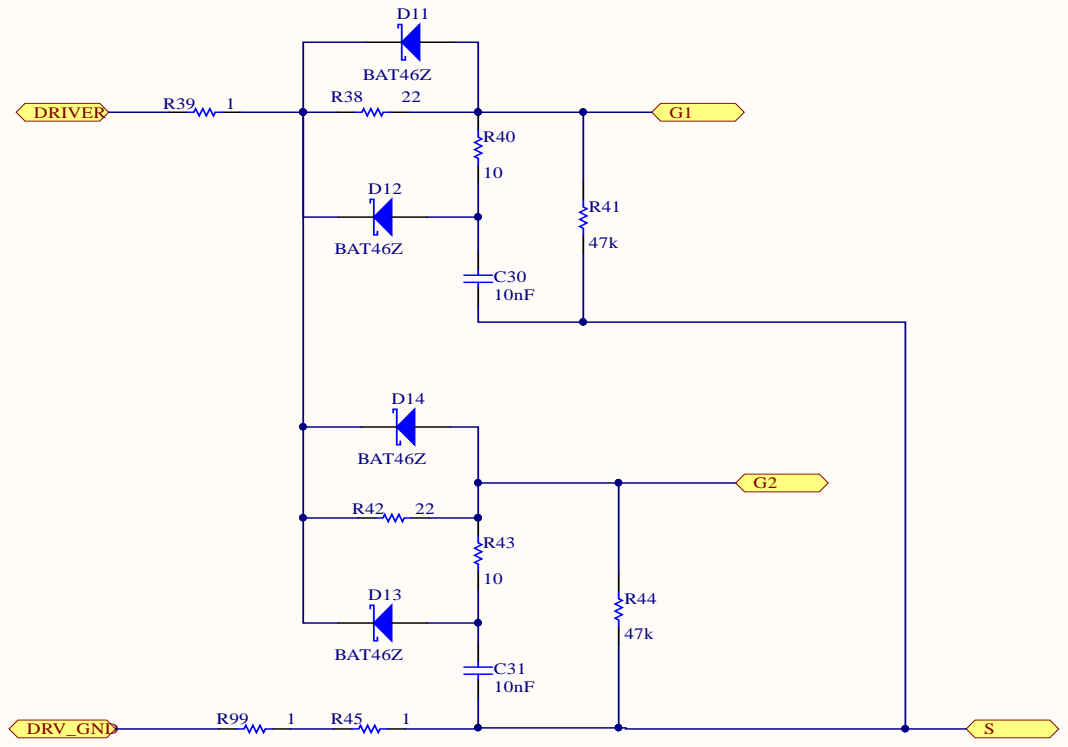
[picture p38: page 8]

Gate drive circuit Inverter_LCEE.PrjPcb

UNICAMP / LCEE
University of Campinas - Brazil

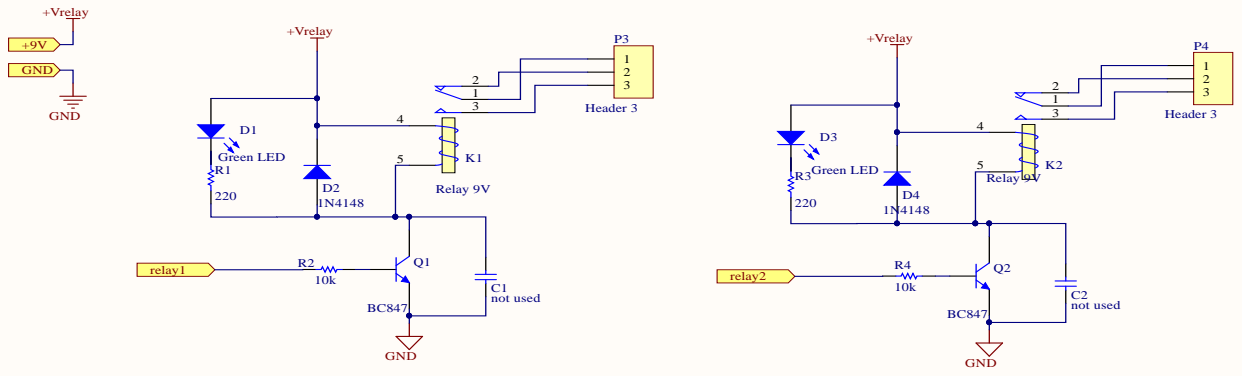
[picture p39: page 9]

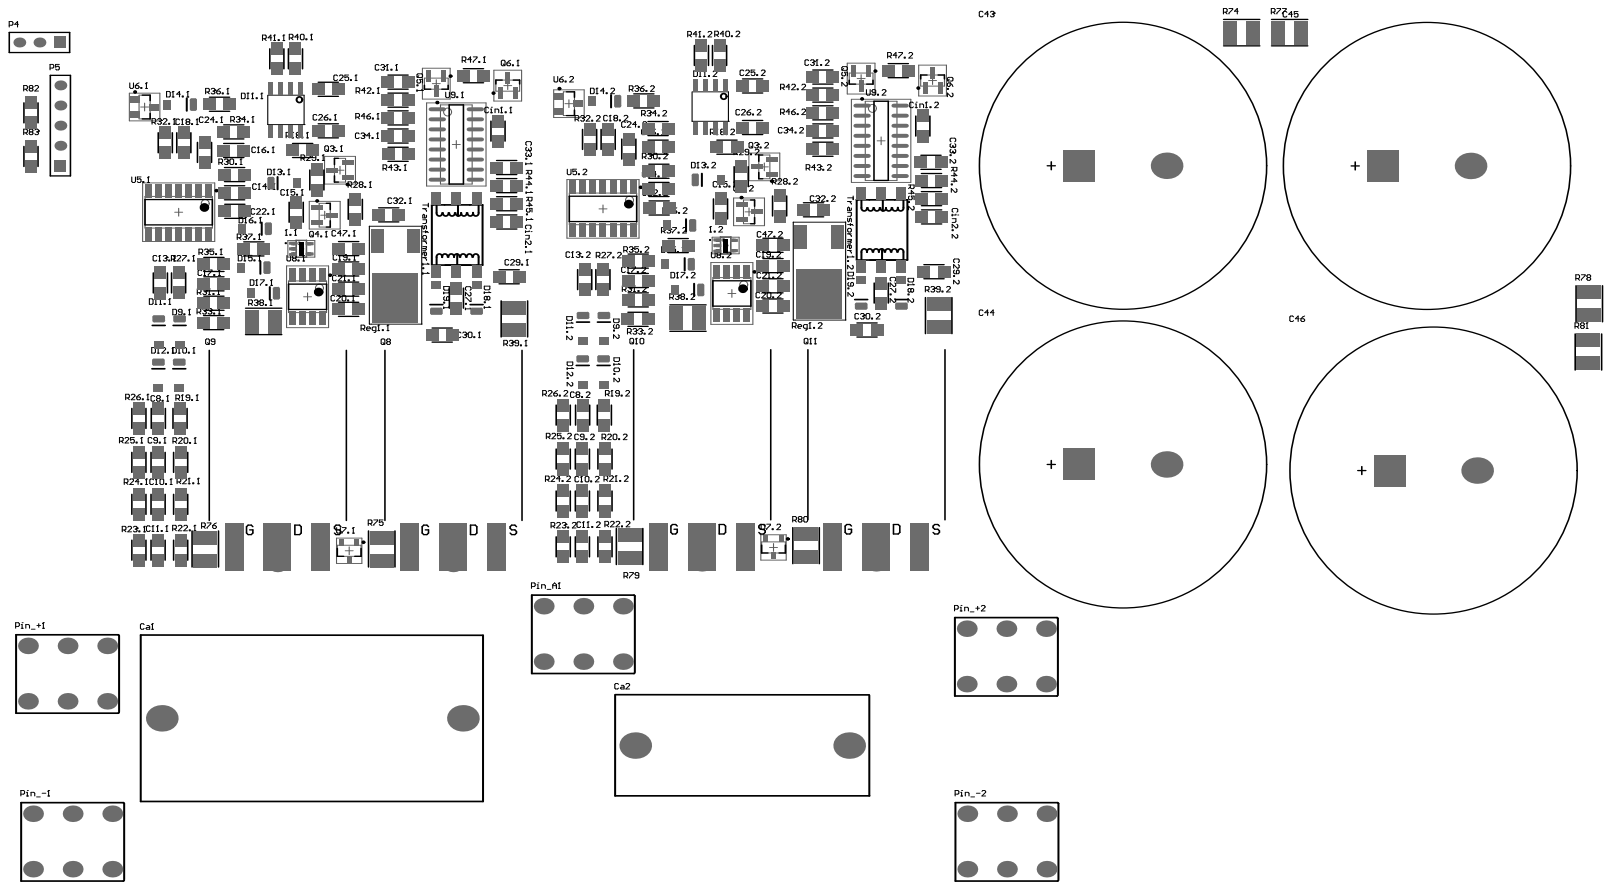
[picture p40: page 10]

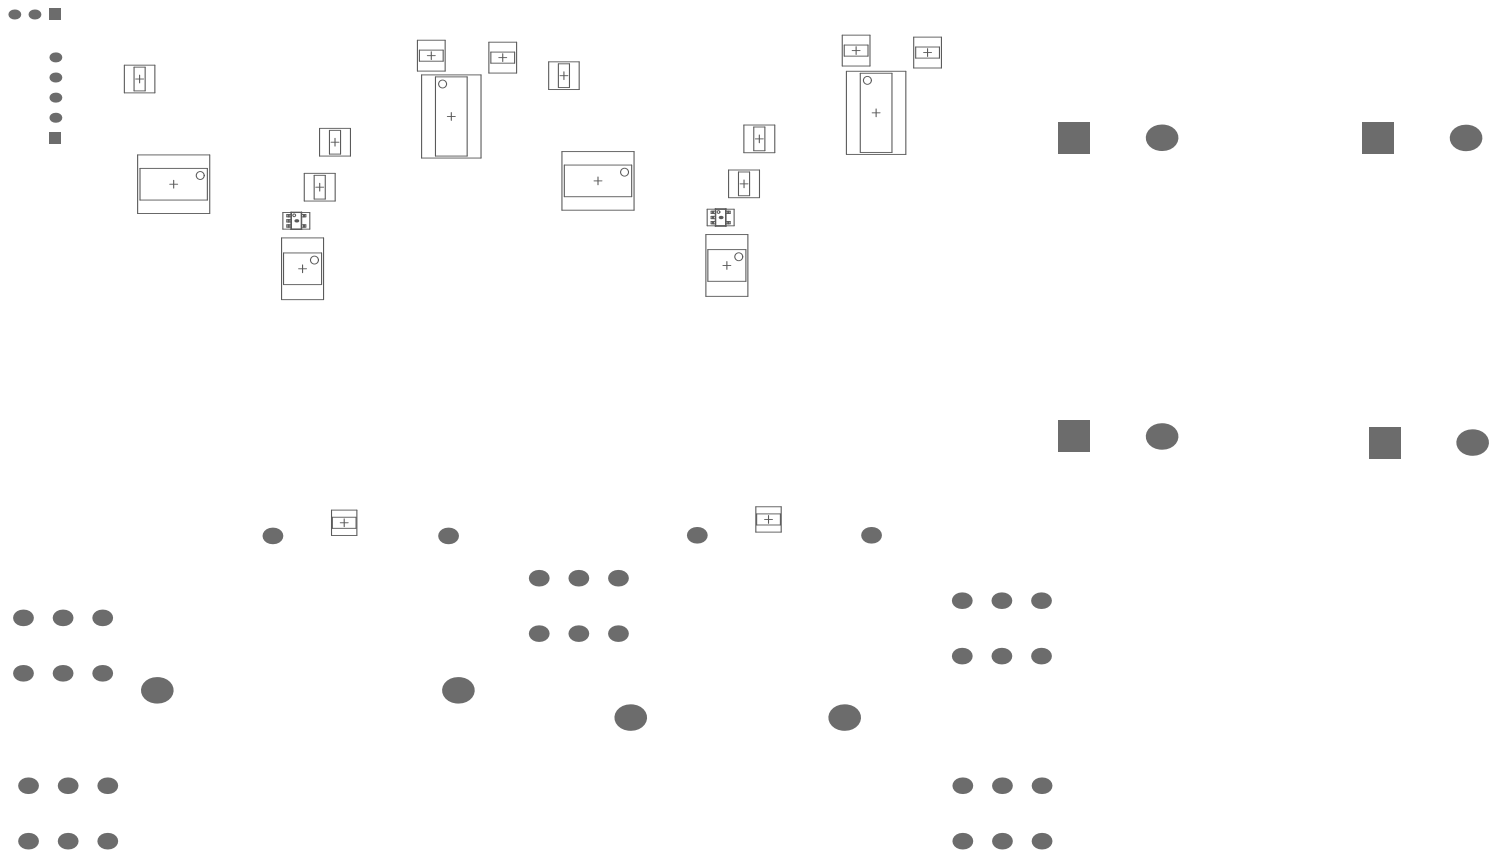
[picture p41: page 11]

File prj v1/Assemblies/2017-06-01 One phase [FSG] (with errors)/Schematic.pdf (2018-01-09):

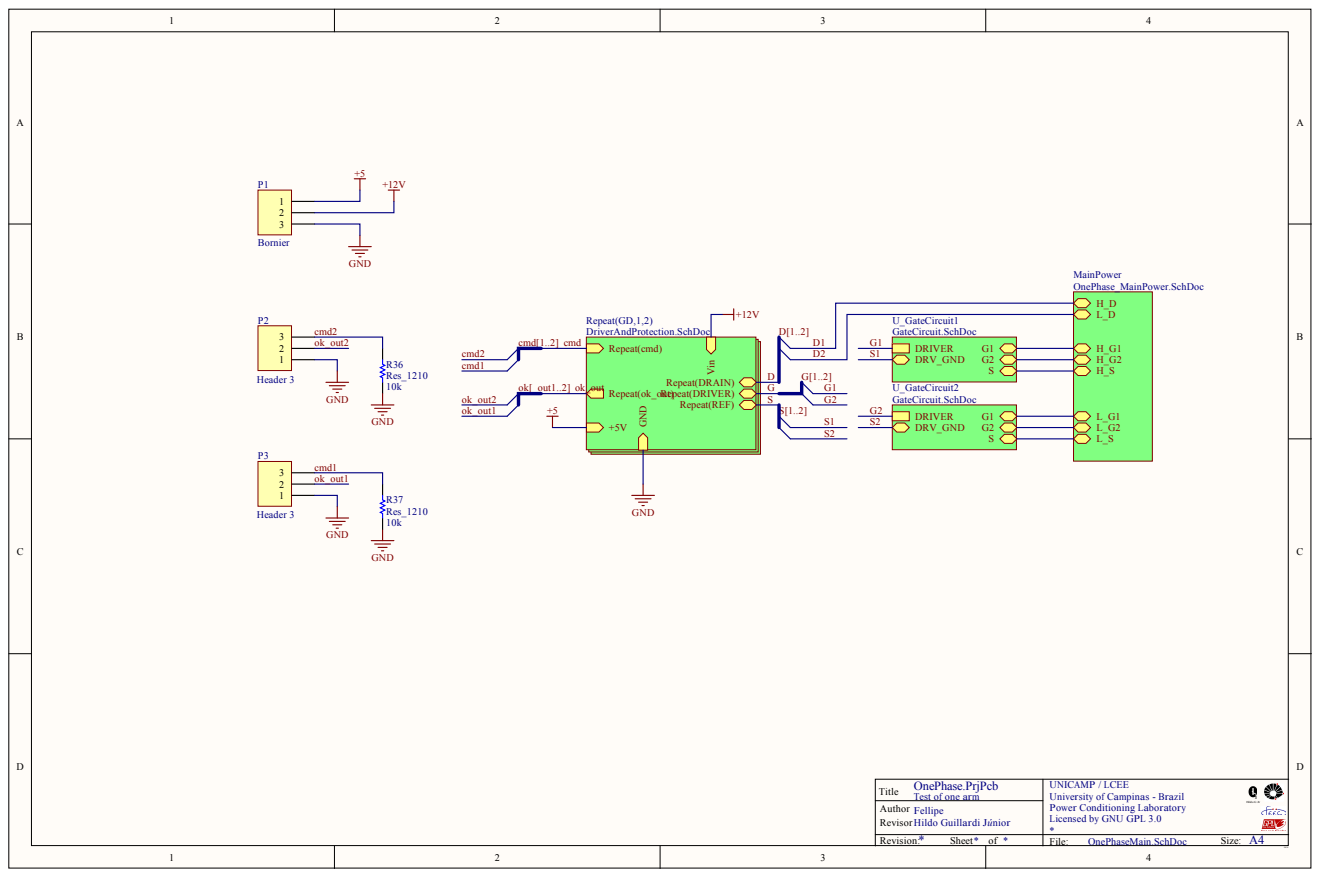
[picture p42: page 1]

D | DRV _ G N D G 2


Current Protection (using Vds voltage drop)

Temperature Protection (sensor close to MOSFET drain)

The OA input "+" / "-" and changed in U1C and U1D.
Felipe put this error also in the Layout.
"Give a way" on the assembly.

Drive and protections OnePhase.PrjPcb

UNICAMP / LCEE
University of Campinas - Brazil
Power Conditioning Laboratory
Licensed by GNU GPL 3.0


Isolated power supply OnePhase.PrjPcb

UNICAMP / LCEE
University of Campinas - Brazil
Power Conditioning Laboratory
Licensed by GNU GPL 3.0


Gate drive circuit OnePhase.PrjPcb

UNICAMP / LCEE
University of Campinas - Brazil
Power Conditioning Laboratory
Licensed by GNU GPL 3.0





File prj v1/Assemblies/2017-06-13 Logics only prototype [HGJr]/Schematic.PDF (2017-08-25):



Main power supply LogicsOnly.PrjPcb

UNICAMP / LCEE
University of Campinas - Brazil
Power Conditioning Laboratory
Licensed by GNU GPL 3.0


Relay fault behaviour:
Connnecting the jumper make the
relays open in a fault event.

Reset behaviour:
First: disable the board
Second: pulse the reset

OE3 10
OE4 13

fault

fault-reset' is active LOW

Protection Interlock
Connect jumpers to interlock
phase protection

Logic circuits LogicsOnly.PrjPcb

UNICAMP / LCEE
University of Campinas - Brazil
Power Conditioning Laboratory
Licensed by GNU GPL 3.0


Dead time & interlock LogicsOnly.PrjPcb

UNICAMP / LCEE
University of Campinas - Brazil
Power Conditioning Laboratory
Licensed by GNU GPL 3.0




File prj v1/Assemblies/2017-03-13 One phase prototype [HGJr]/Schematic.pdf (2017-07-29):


Conferir lógica
Sensor de temperatura (i2c)
Alimentação para cooler (PWM?)
Melhorar apresentação / Deixar diagramas mais "didáticos"
(colocar descrições, instruções de ajuste, nomes, organização dos blocos etc)
Iniciar Layout
Definir conectores e fixações (projeto mecânico)
Definir disspador / cooler (projeto térmico)
Fabricação Placas de testes
Início dos testes

Author:
Arthur Crisóstomo Prates
License under GNU-GPL 3.0


Proteção de corrente (por tensão de condução)

Proteção de tensão de desligamento

Proteção de temperatura da junção (por temperatura no dreno)

Author:
Fellipe Saldanha Garcia
License under GNU-GPL 3.0


5V_ref | - IN 2 15 +IN 2 16

C31 | D-T CON 4

Author:
Hildo Guillardi Júnior
Joel Filipe Guerreiro
Fellipe Saldanha Garcia
Arthur Crisóstomo Prates
License under GNU-GPL 3.0


Author:
Hildo Guillardi Júnior
License under GNU-GPL 3.0


Author:
Hildo Guillardi Júnior
License under GNU-GPL 3.0


Author:
Hildo Guillardi Júnior
License under GNU-GPL 3.0


Author:
Hildo Guillardi Júnior
License under GNU-GPL 3.0

# Board S


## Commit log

2017-08-14 Fixed connections
    Fixed the wrong connections of the gate drive protection.
    Updated the gate circuit values.
    Did the main to the full project.
    [Auxiliary.SchDoc, DriverAndProtection.SchDoc, Inverter_LCEE.SchLib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]
2017-08-16 Full inverter schematic
2017-08-16 Full inveter schematic
    Did the full inverter schematic (not layout yet)
    Sheet standard with the GNU GPL 3.0 license
    [Auxiliary.SchDoc, Conectors_IsolatedSupply.SchDoc, DeadTimeDriver_Leg.SchDoc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]
2017-08-25 Fixed rooms
    Fixed rooms and university machine requirements
    [LogicsOnly.GBL, LogicsOnly.GBS, LogicsOnly.GKO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]
2017-08-25 Fixed logic PCB board
    Fixed rooms
    Fixed university machine requiments
    [LogicsOnly.PcbDoc]
2017-08-31 Fix the main supply components values
    [MainPowerSupply.SchDoc]
2018-01-08 Updated template and manf codes
    [Auxiliary.SchDoc, Conectors_IsolatedSupply.SchDoc, DeadTimeDriver_Leg.SchDoc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]
2018-01-08 Updated manf
    [Conectors_IsolatedSupply.SchDoc, DeadTimeDriver_Leg.SchDoc, DriverAndProtection.SchDoc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]
2018-01-08 Updated BOM
    [Auxiliary.SchDoc, DeadTimeDriver_Leg.SchDoc, LogicsOnly_Main.SchDoc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]
2018-01-09 Added all manf codes
    [Auxiliary.SchDoc, Conectors_IsolatedSupply.SchDoc, DeadTimeDriver_Leg.SchDoc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]
2018-01-10 manf# codes
    [DriverAndProtection.SchDoc, Inverter_LCEE.PrjPcb, IsolatedPowerSupply.PrjPCB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]
2018-01-11 BOM with cost
    [Inverter_LCEE.xlsx, IsolatedPowerSupply.xlsx, LogicsOnly.xlsx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]
2019-01-28 Luis project
    [Analog_protections.SchDoc, Analog_voltage_reference.SchDoc, DC_link_input.SchDoc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]
2019-01-28 V1 project (Arthur + Felipe)
    [AQAC.SCHLIB, AQAC_1.SCHLIB, Auxiliary.SchDoc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]
2019-05-09 Sync local files
    [AQAC.SCHLIB, AQAC_1.SCHLIB, Analog_protections.SchDoc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]
2019-05-09 Add BOM
    [IsolatedPowerSupply.xlsx, LogicsOnly.xlsx, OnePhase.xlsx]
